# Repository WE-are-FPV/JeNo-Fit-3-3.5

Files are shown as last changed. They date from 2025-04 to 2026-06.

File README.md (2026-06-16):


> [!NOTE]
> Current version : **1.0.0** (read [changelog](#changelog) for details)

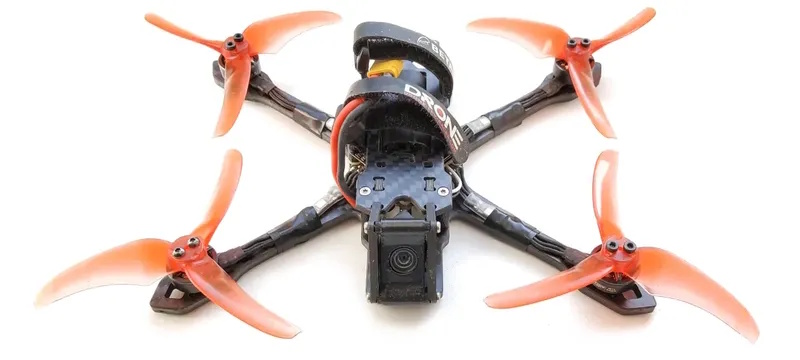
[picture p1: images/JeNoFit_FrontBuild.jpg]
JeNo Fit


# JeNo Fit 3 and 3.5"
***3 and 3.5" drone FPV frame compatible with Air Unit O4 Lite (or any Nano camera), designed for Freestyle, Freeride, bando and Cinematic.***

> [!NOTE]
> Designed in France by members of the [WE are FPV](https://www.wearefpv.fr/) community, the JeNo is already flown by hundreds of pilots and is now being sold by [Drone FPV Racer](https://www.drone-fpv-racer.com/recherche?controller=search&s=JeNo+5.1+frame&aff=64&id_campaign=13) (affiliate link). The French version of the project is available on [Printables](https://www.printables.com/model/1236372-jeno-fit-335-drone-frame). Note that a [2.5" version](https://github.com/WE-are-FPV/JeNo-Pocket), a [3-3.5" version for O4 Pro](https://github.com/WE-are-FPV/JeNo-3-3.5), a [5.1-6" version](https://github.com/WE-are-FPV/JeNo-5.1) and a [7-8" version](https://github.com/WE-are-FPV/JeNo-7) of the JeNo exist.

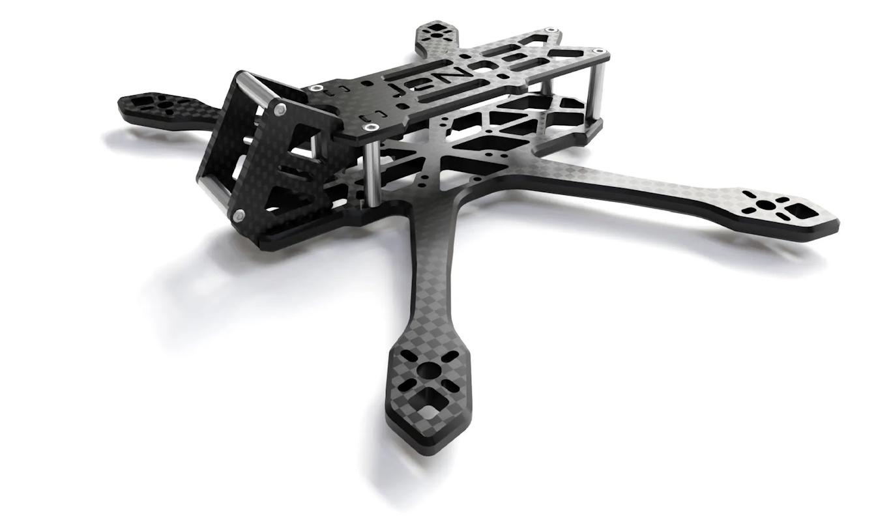
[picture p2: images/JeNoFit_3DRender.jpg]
JeNo Fit - 3D render


## Table of contents

* [Key features](#key-features)
* [Presentation](#presentation)
* [A frame available in 3 versions](#a-frame-available-in-3-versions)
* [Detailed specifications](#detailed-specifications)
* [Design: 16mm bus height – AIO only](#design-16mm-bus-height-aio-only)
* [Strategy / Motorization / Weight](#strategy-motorization-weight)
* [Blackbox](#blackbox)
* [Sturdiness](#sturdiness)
* [Versions and files](#versions-and-files)
* [Get it cut !](#buy-it-or-cut-it-)
* [Bill of materials](#bill-of-materials)
* [Inspiration](#inspiration)
* [Tuning, Betaflight Preset](#tuning-betaflight-preset)
* [Builds examples](#builds-examples)
* [Authors](#authors)
* [TPU](#tpu)
* [Community (remixes and TPU)](#community-remixes-and-tpu)
* [Changelog](#changelog)

## Key features
- [x] Perfect integration of the **DJI Air Unit O4 Lite camera**
- [x] **Wide-X** geometry
- [x] Excellent flight **performance**, easy to tune
- [x] **Sturdiness/rigidity** with a 4mm bottom plate
- [x] **100% unobstructed FOV**: Frame and standoffs invisible in the video feed
- [x] Designed for: DJI AU O4 Lite, Naked Vista (with Nebula Pro Nano), WalkSnail single board, HDZero single board, Analog
- [x] **Compact**... but not too much...
- [x] Obviously **Open Source**

## Presentation
The **DJI O4 Lite** opens up new possibilities for the 3" format: 100g builds (excluding the lipo) are once again easily achievable, with a shorter, lower, **sleeker**, and stronger frame.

The camera cage of the **JeNo Fit 3"** will therefore be designed for **Nano-sized cameras**, meaning **14mm**. 16mm standoffs slot into 1mm-deep pockets.

Of course, if you want to use an O3 or an O4 Pro, you'll need to stick with the standard [JeNo 3-3.5"](https://github.com/WE-are-FPV/JeNo-3-3.5).

But if you're ready for an O4 Lite, or even a Naked Vista, then this little JeNo Fit 3/3.5 will be much more optimal!

A small comparison between a lightweight JeNo 3" (on the right), and this new JeNo Fit 3" (on the left):
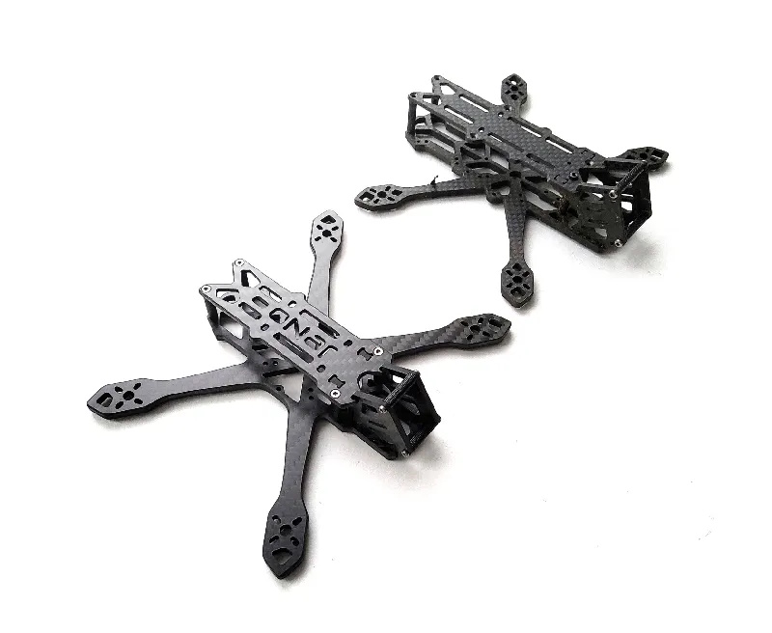
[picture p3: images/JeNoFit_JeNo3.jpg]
JeNo Fit, Fit vs Classic 3"


The JeNo is also available in [2.5" version](https://github.com/WE-are-FPV/JeNo-Pocket), [3" and 3.5" versions for O3/O4 Pro](https://github.com/WE-are-FPV/JeNo-3-3.5), [5.1-6" versions](https://github.com/WE-are-FPV/JeNo-5.1) and [7-8" versions](https://github.com/WE-are-FPV/JeNo-7).

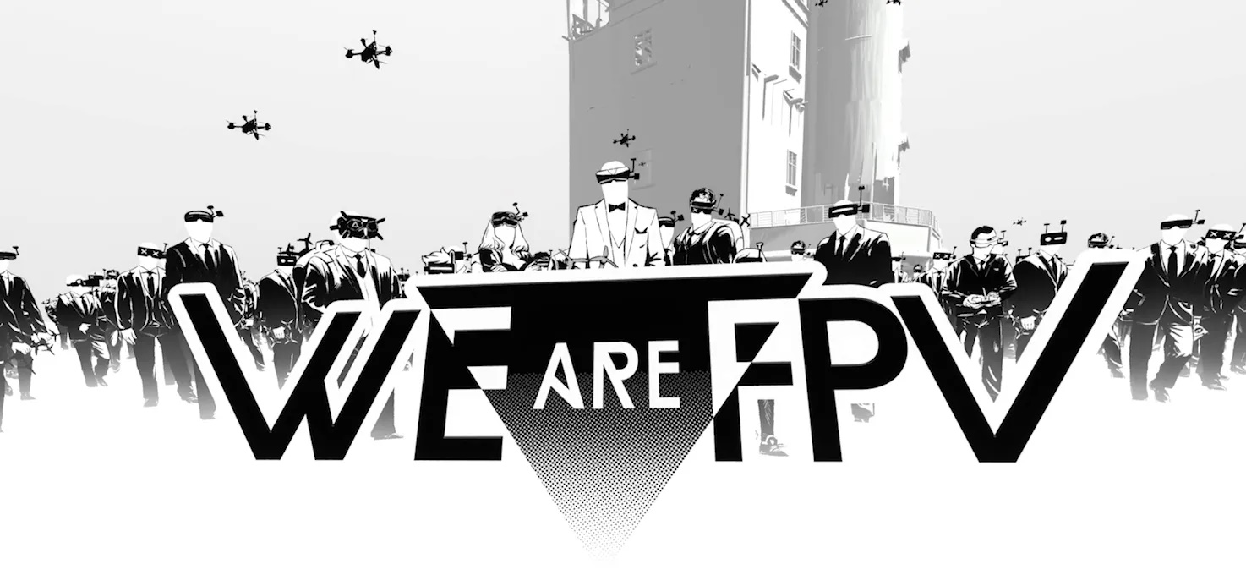
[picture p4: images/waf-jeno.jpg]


## A frame available in 3 versions
The frame is available in the following versions:

* **3.5" :** 40g with titanium screws
* **3.5" light :** 36g with titanium screws
* **3" :** 38g with titanium screws

At launch, the included **camera plates** are designed for a **30° tilt**. Other camera plates will likely be added soon (25° and 40°).

## Detailed specifications

|||
| :--- | :--- |
| **Geometry** | **Wide-X** | 
| **Props size** | 3 to 3.5" depending on the version | 
| **Weight** | **35 to 40g** depending on the version, with titanium screws | 
| **Body height** | 16 mm M2 | 
| **Bottom plate** | **4 mm** unibody | 
| **Top plate** | 2 mm | 
| **Camera plates** | 2.5 mm | 
| **Motors mounting** | 9-12 mm | 
| **Camera** | 14 mm, Nano, O4 Lite camera. **Clear FOV**. (16mm standoffs recessed) |
| **Main stack** | AiO 25.5 mm x 25.5 mm (M2) and 20 mm x 20 mm (M2) | 
| **Supported VTX** | Analogic, **DJI Air Unit O4 Lite**, WalkSnail, HDZero… | 
| **Strap passage** | Yes | 

## Design: 16mm bus height – AIO only
For the electronics, only AiOs will be accepted. However, they can have the USB port either horizontally or vertically, while keeping the USB port protected.

There will be enough space for an external RX and/or capacitor at the rear and front.

For builds using a Naked Vista, it is recommended to tape the underside of the top plate to prevent short circuits due to contact with the carbon (the build remains relatively tight).

AiO with vertical USB: (AiO rotated 90°)

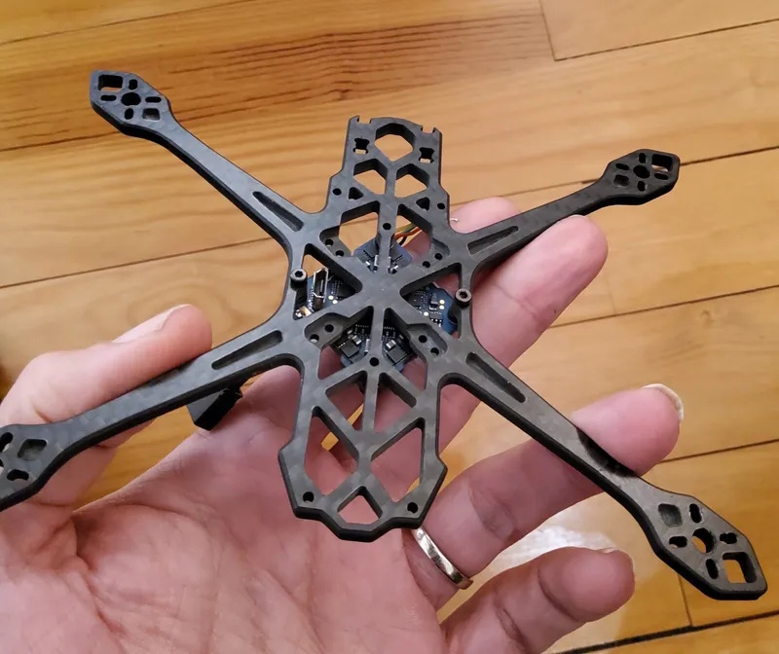
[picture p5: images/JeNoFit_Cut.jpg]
JeNo Fit, RX options


| 3" Naked Vista build | 3.5" O4 "light" build |
| :---: | :---: |
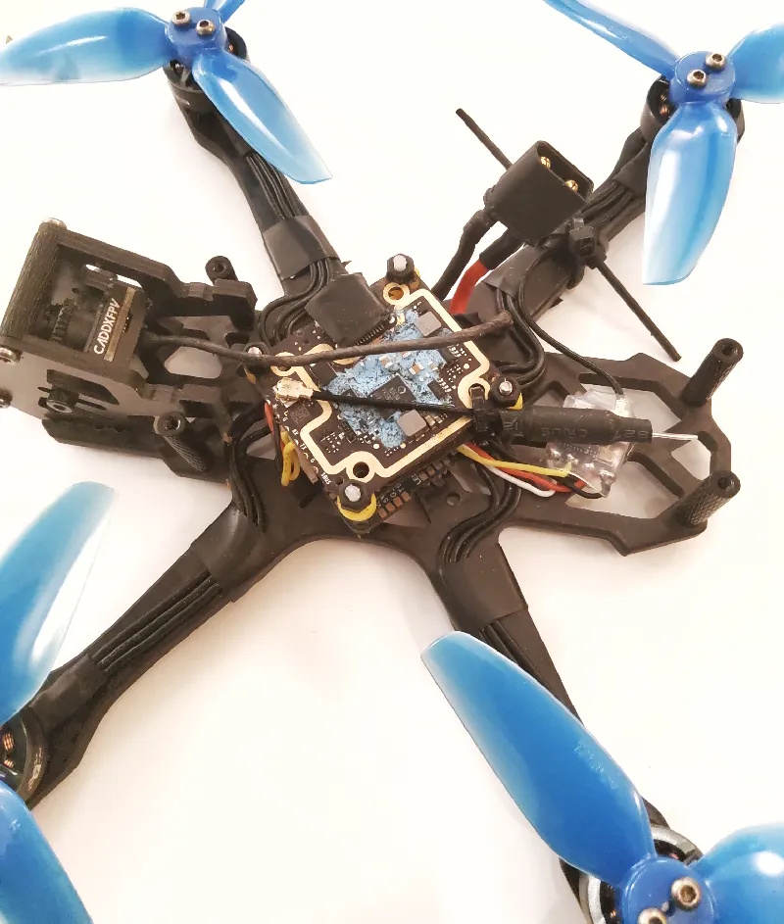
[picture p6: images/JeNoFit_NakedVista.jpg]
Freestyle camera plates
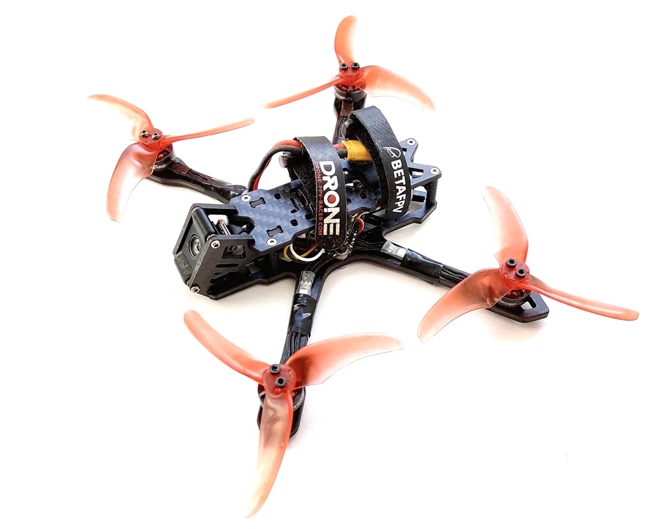
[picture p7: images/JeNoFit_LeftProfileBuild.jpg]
Cinematic camera plates
|  |  |

## Strategy / Motorization / Weight

Several strategies are available to you:

* **3" or 3.5"**, with a wide range of motor options depending on what you want to achieve: from **1204 to 1604**. This choice will have a significant impact on the build's weight, behavior, and flight time.
* If you're looking for **discretion** while maintaining optimal cruising speed, the 1204 will be perfect in **3.5"**, between **5000 and 6000kv** for **3S**. The sound of the Emax Avan 3528 props will remain discreet at lower RPMs.
* If you're after **punch, the **1604** should be perfect for **4S**.
  * **1604 = 46g** motors
  * **1204 = 24g** motors

| 1204 | 1404 | 1604 |
| :---: | :---: | :---: |
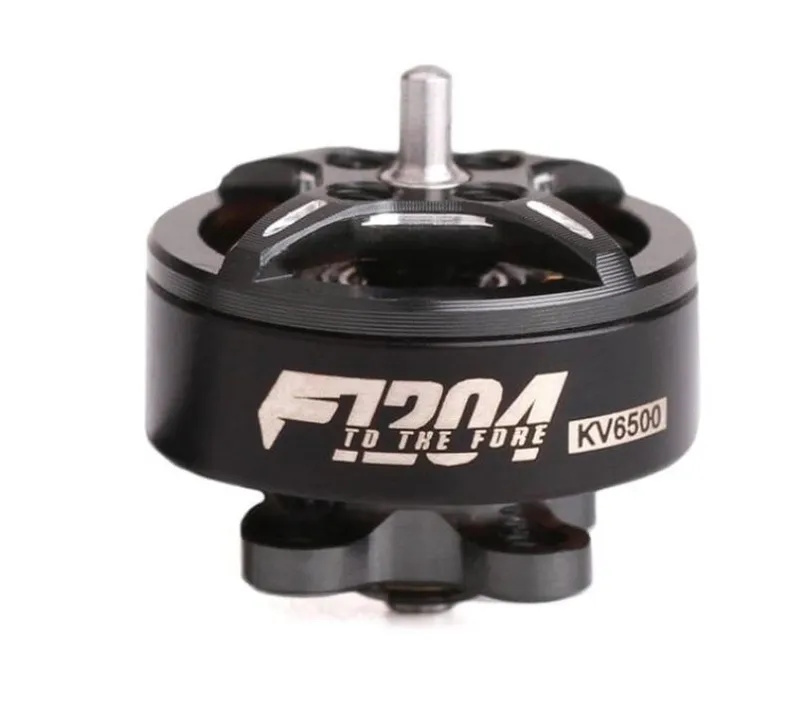
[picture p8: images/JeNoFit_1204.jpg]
1204 motor
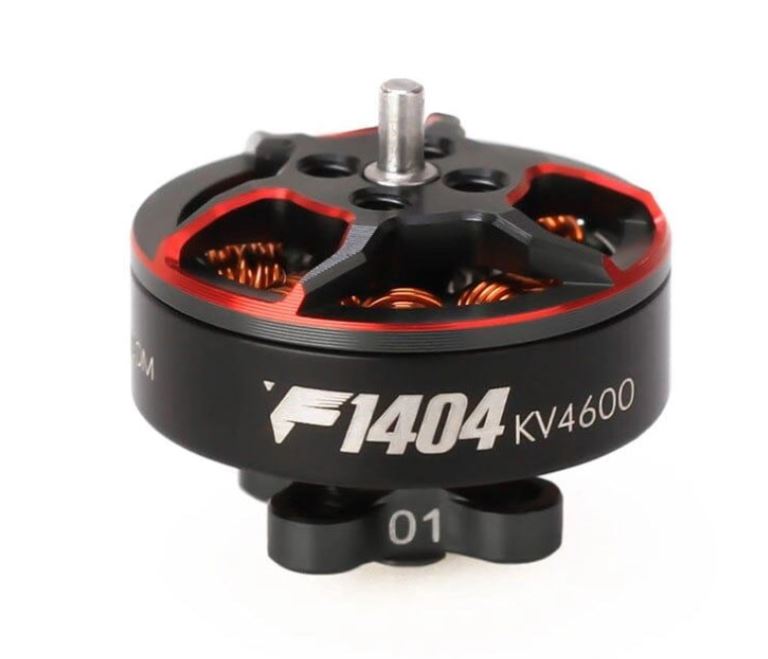
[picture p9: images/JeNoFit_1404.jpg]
1404 motor
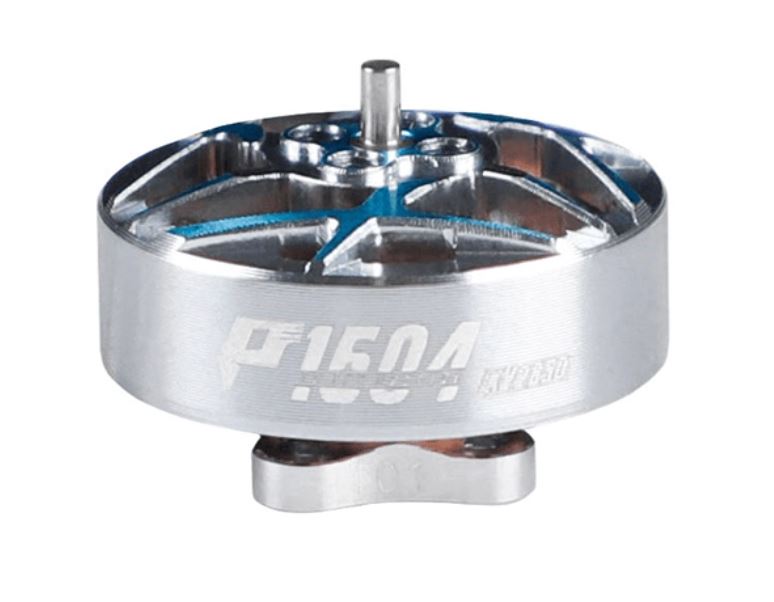
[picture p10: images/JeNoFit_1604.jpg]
1604 motor
|  |  |  |
| 6.9gr (incl cable) | 9.3gr (incl cable) | 11.6gr (incl cable) |

You will therefore be looking at a build around 95/100g with 1204 motors, versus 122g with 1604 motors.

1204 and Naked Vista build at 99g:
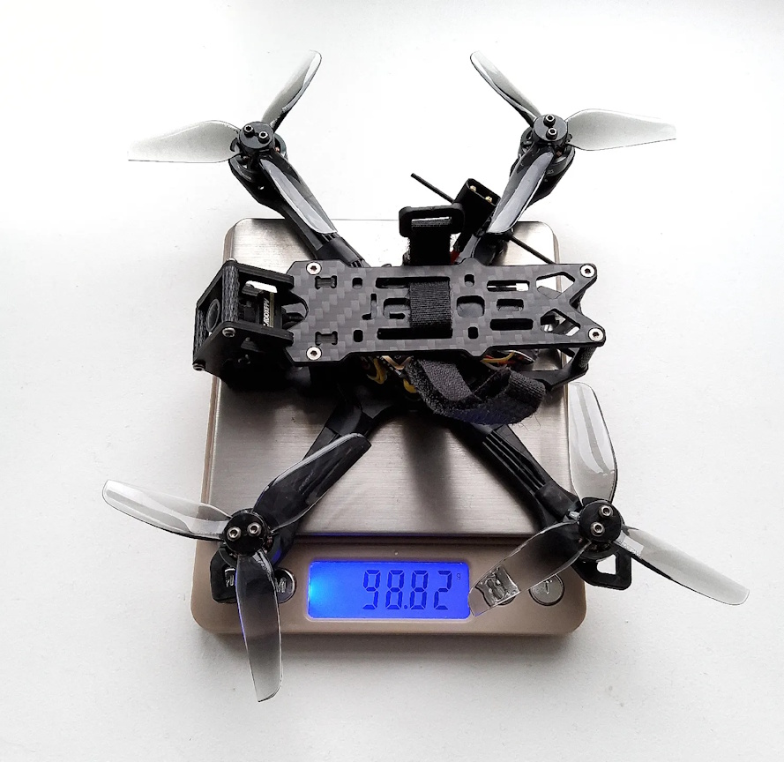
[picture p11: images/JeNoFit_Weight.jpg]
JeNo Fit weight
  |
 
## Blackbox

The 4mm bottom plate ensures a clean BB.

Here is an excerpt of the BB in 3.5" / 1204:

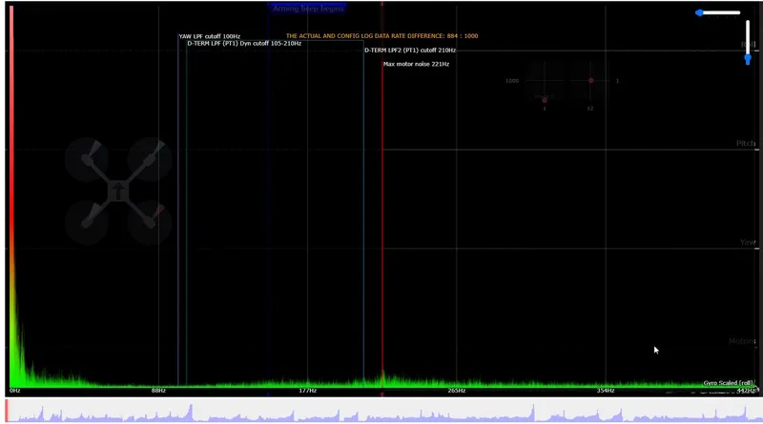
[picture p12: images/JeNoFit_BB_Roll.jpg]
JeNo Fit Blackbox roll

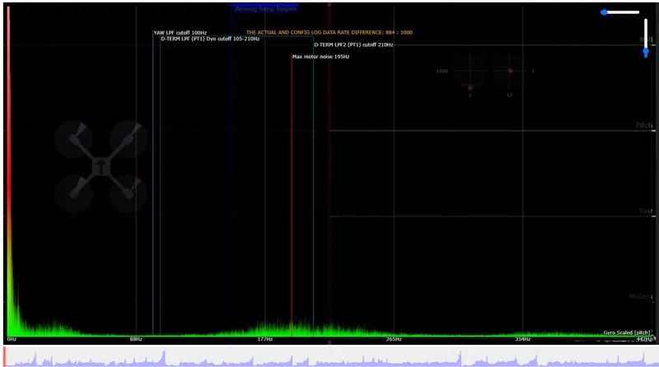
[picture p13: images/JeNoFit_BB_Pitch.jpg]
JeNo Fit Blackbox pitch

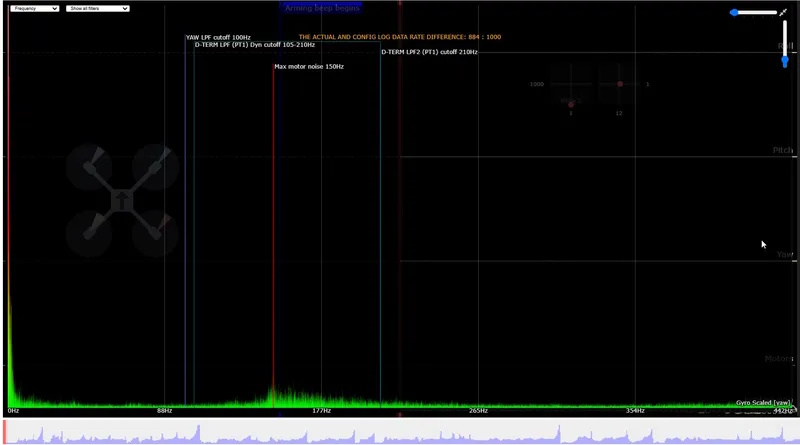
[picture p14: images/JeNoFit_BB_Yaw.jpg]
JeNo Fit Blackbox yaw


## Sturdiness
The build is **lighter** than a standard JeNo 3. The **bottom is shorter** but still **4mm** thick, so we’re not concerned about the frame's durability. Remember to grab the arm protection from the [JeNo 3"](https://github.com/WE-are-FPV/JeNo-3-3.5) if you're doing bando.

## Versions and files

### Versioning
You will find the **current version** of the frame at the beginning of the description and the full [history of modifications](#changelog) at the end of the page.

We strongly recommend always cutting the latest version to ensure you benefit from the most recent optimizations.

The version **number format** is as follows :
```
<Major versions>.<Minor version>.<Revision>
ex : 1.3.2
```

* **Revision :** This number is incremented in the case of minor modifications with no significant impact.
* **Minor version :** This number is incremented for minor modifications that may potentially break compatibility with certain TPU parts.
* **Major version :** This number is incremented for significant modifications that break compatibility at the carbon level.

Since the creation of the JeNo 5", we have always strived to **maintain compatibility at the carbon level**. As a result, the version remains “1.x.y.”

**Note :** If you develop TPU parts for the JeNo, be sure to specify the version they are compatible with.

### Files management
To simplify things, we have reorganized the file structure. The files are now divided into **five groups** :

* **01-FRAME :** Contains **models** describing the **frame** in DXF, STEP, and STL formats for the current version. Also contains a PDF file which is a reformatted version of the DXF.
* **02-TPU :** Contains **TPU models** for the current frame version in STL format.
* **03-FRAME-HISTORY :** Contains previous versions of the frame.
* **04-TPU-HISTORY :** Contains TPU models that are no longer compatible with the current version.
* **OTHER-FILES :** Contains documentation files, including the assembly manual and a description.

The major change is that all options are now consolidated into a single file. This will make version management significantly easier for us.

If you want to view the DXF file with all annotations, we recommend using the free software [DWG TrueView](https://www.autodesk.com/products/dwg-trueview/overview). If you prefer not to use it, the PDF version of the file will contain all the necessary information.

## Get it cut !

JeNo Fit, cut

The JeNo Fit 3/3.5" is available at [FPV CNC Drone](https://fpvcncdrone.com/).

Unlike the 3 and 5" JeNos, the JeNo Fit won't be available in shops.

The ["01-FRAME"](https://github.com/WE-are-FPV/JeNo-Fit-3-3.5/tree/main/01-FRAME) folder contains all the files you need to get it **cut**. .DXF and .STEP files are available.

## Bill of materials

In addition to the carbon fiber, you will need the following hardware to complete the assembly of the frame.

**Standoffs**

It is recommended to use 5mm diameter standoffs, especially for those that will serve as support for TPU (backpack and capacitor). Moletted spacers can still be used, but the TPU supports will need to be modified accordingly.

| Quantity | Description | Details |
| :---: | :--- | :--- |
| **4** | **M2x16mm** standoffs **(4 mm diameter)** | for the body |
| **2** | **M2x16mm** standoffs **(4 mm diameter)** | for the camera (14mm) |

> [!NOTE]
> The standoffs for the camera plates are recessed by 1mm on each side to standardize the hardware. If you have 14mm standoffs, you can use them by having custom camera plates made without the 1mm pockets.

**Stack materials**

20mm screws will comfortably accommodate most configurations. You can use shorter screws if you prefer.
| Quantity | Description | Details |
| :---: | :--- | :--- |
| **4** | **M2x16/18mm** screws | for the stack |
| **8** | **M2** nylon nuts for the stack screws (4 nuts for the base, 4 nuts on top) | for the stack |

**Frame materials**

| Quantity | Description | Details |
| :---: | :--- | :--- |
| **4** | **M2x6/8mm countersunk screws** (titanium if possible) | for the top plate |
| **8** | **M2x8mm screws** screws (titanium if possible) | for the bottom and camera plates |

**Additional materials**

| Quantity | Description | Details |
| :---: | :--- | :--- |
| **12-16** | **M2x6mm** screws if there is NO arm protection between the screw and the motor, otherwise, **M2x7mm**. To save **weight**, you can use only **3 screws per motor**. | for the motors |

## Inspiration

The **JeNo Fit** is primarily inspired by its bigger brother, the [standard JeNo 3"](https://github.com/WE-are-FPV/JeNo-3-3.5). Like the [JeNo Fit](https://github.com/WE-are-FPV/JeNo-Pocket), it is designed for a Nano-sized camera.

**Gone is the rear stack**, which is no longer needed with the Air Unit O4 Lite. The front, made up of 2 camera plates, was designed around the O4 Lite camera.

## Tuning, Betaflight Preset

**No preset integrated for now.** The behavior of the AiOs can vary quite a bit from one to another. We’ll wait for more feedback.

However, here’s an overview of the first tune used for our test flights, which you can use as a starting point if your **Blackbox is clean enough**. Note that we’ve activated the profile switch based on the number of cells in the lipo.

As always, be very **cautious** when applying these settings.

## Builds examples

You can find several build examples in the Dronebuilds section of the WE are FPV forum:

* [Jeno 3 Low Profil O4](https://forum.wearefpv.fr/topic/24231-jeno-3-low-profil-o4) (by Tooks)

## Authors

The JeNo Fit was designed by :

* nochamo - [Youtube](https://www.youtube.com/user/nochamo)

## TPU

Among the files to download, you’ll find some TPU parts for your JeNo Fit. Initially, these include only the camera/antenna mounts for 4 mm standoffs.

## Community (remixes and TPU)

**Fork/remix**

If something isn't 100% to your liking on the JeNo Fit, feel free to check out the community remixes—you might just find what you're looking for:

**TPU**

## Changelog

> [!TIP]
> Compatibility is consistently maintained between each version: if your frame was a v1, the parts from v1.2 will be compatible. The same applies to TPU accessories. That's why we don't keep the history of previous versions.

* Version **1.0.0** (01/02/2025) :
  * Release of the JeNo Fit

## Join the JeNo family !

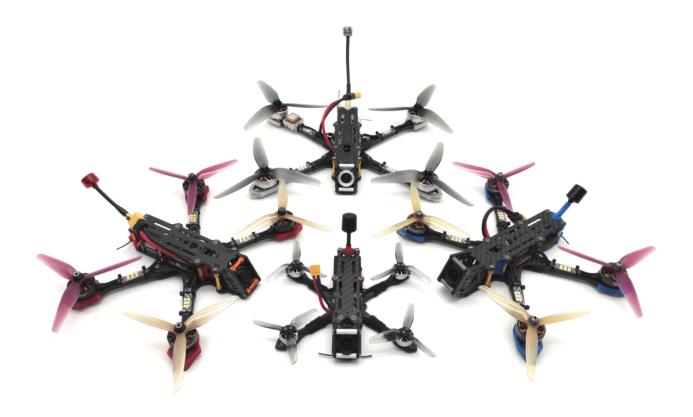
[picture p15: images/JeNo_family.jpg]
||
|:---:|
| JeNo Classic Modus (left), JeNo Cine (right), JeNo 6" (top), JeNo 3" (bottom) |

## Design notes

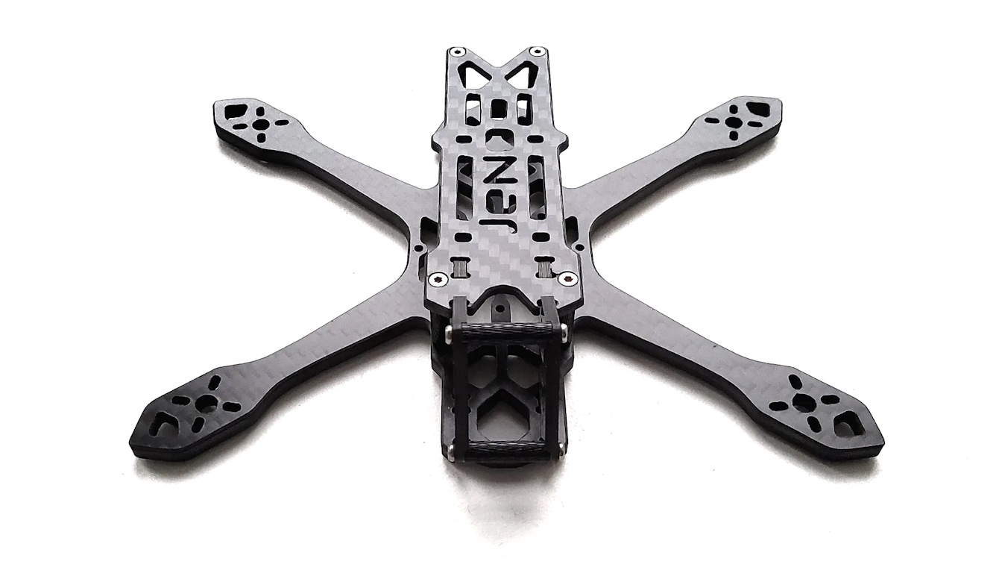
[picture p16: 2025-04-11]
images/JeNoFit_Front.jpg

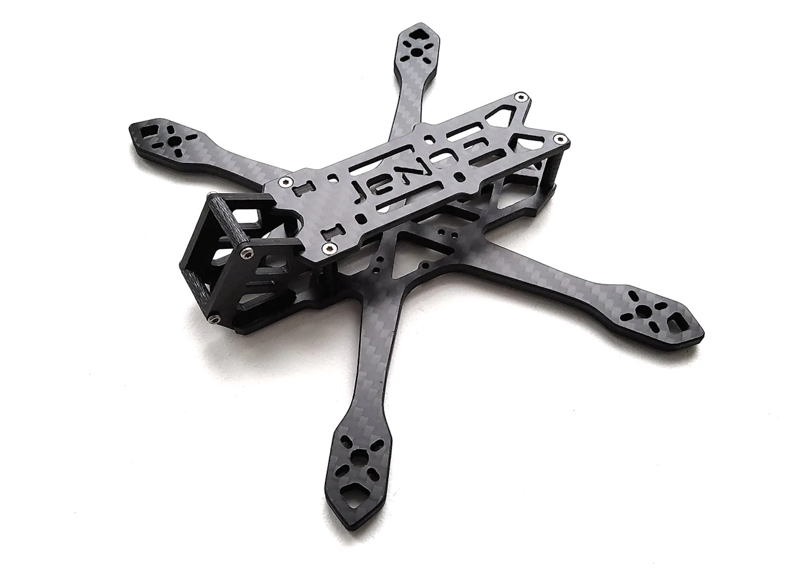
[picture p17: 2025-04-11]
images/JeNoFit_Profile.jpg

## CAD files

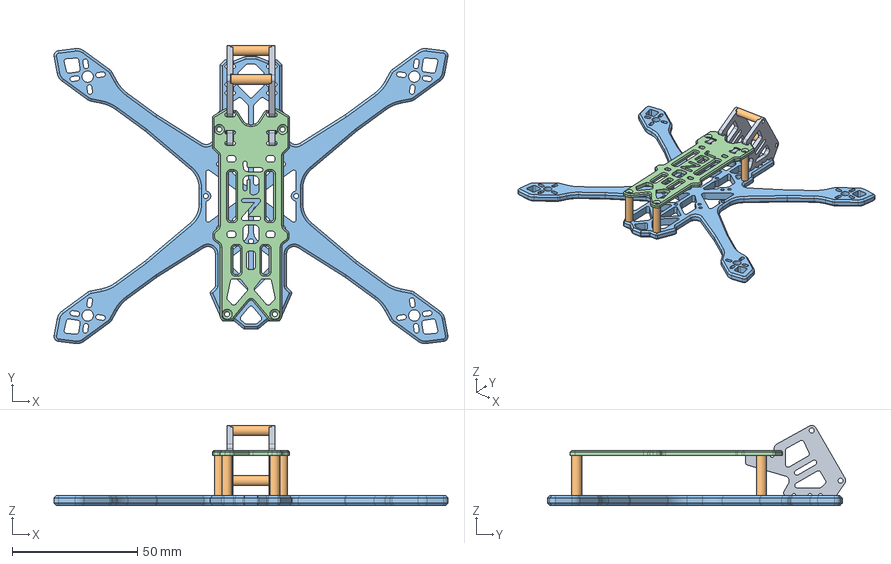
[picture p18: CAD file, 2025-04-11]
01-FRAME/JeNoFit_ALL_VERSIONS_1.0.0.step
157.1 x 118.9 x 31.9 mm

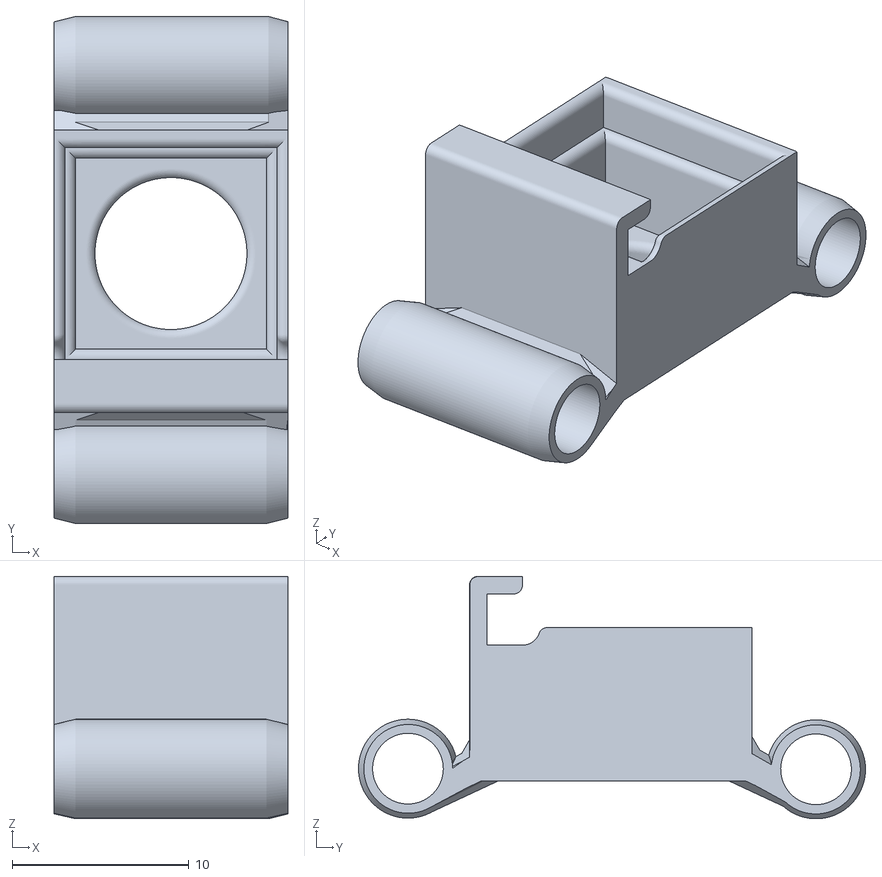
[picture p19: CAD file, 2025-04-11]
02-TPU/JeNoFit_1.0_O4_Lite_Mount_4mm_Standoffs.stl
13.2 x 28.7 x 13.7

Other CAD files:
01-FRAME/JeNoFit_Preview.stl
01-FRAME/JeNoFit_ALL_VERSIONS_1.0.0.dxf

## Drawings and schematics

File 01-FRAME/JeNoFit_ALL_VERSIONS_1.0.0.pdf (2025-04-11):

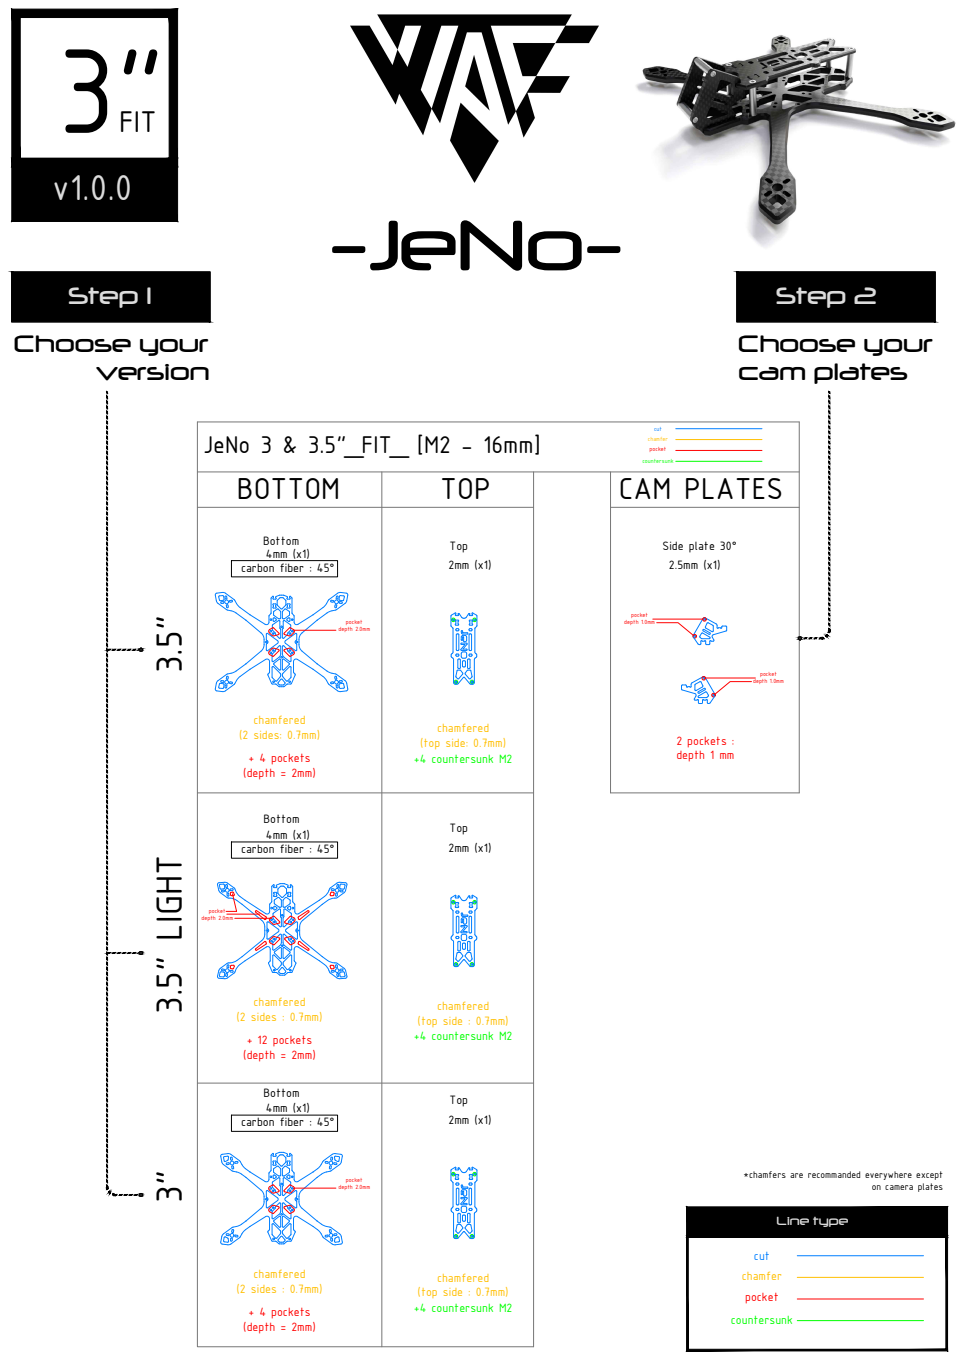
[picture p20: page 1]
(top side: 0.7mm); 2 pockets : depth 1 mm; carbon fiber : 45°; + 4 pockets (depth = 2mm); depth 2.0mm; (2 sides: 0.7mm); +4 countersunk M2; + 12 pockets (depth = 2mm); (2 sides : 0.7mm); (top side : 0.7mm); +4 countersunk M2 3.5" 3.5" LIGHT; 4mm (x1) carbon fiber : 45° 3"; Choose your; Choose your cam plates; Step 1 Step 2; Line type

JeNo 3 & 3.5"_FIT_ [M2 - 16mm] | cut chamfer pocket countersunk
BOTTOM | TOP | CAM PLATES

Bottom 4mm (x1) | Top 2mm (x1) | Side plate 30° 2.5mm (x1) pocket depth 1.0mm pocket depth 1.0mm

*chamfers are recommanded everywhere except

on camera plates

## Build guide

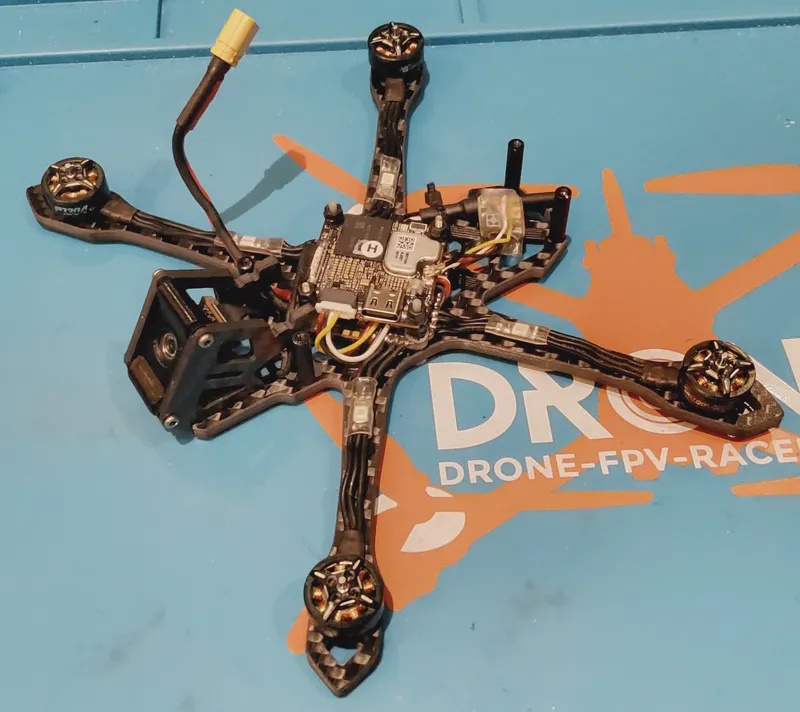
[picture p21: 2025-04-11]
images/JeNoFit_OpenBuild.jpg

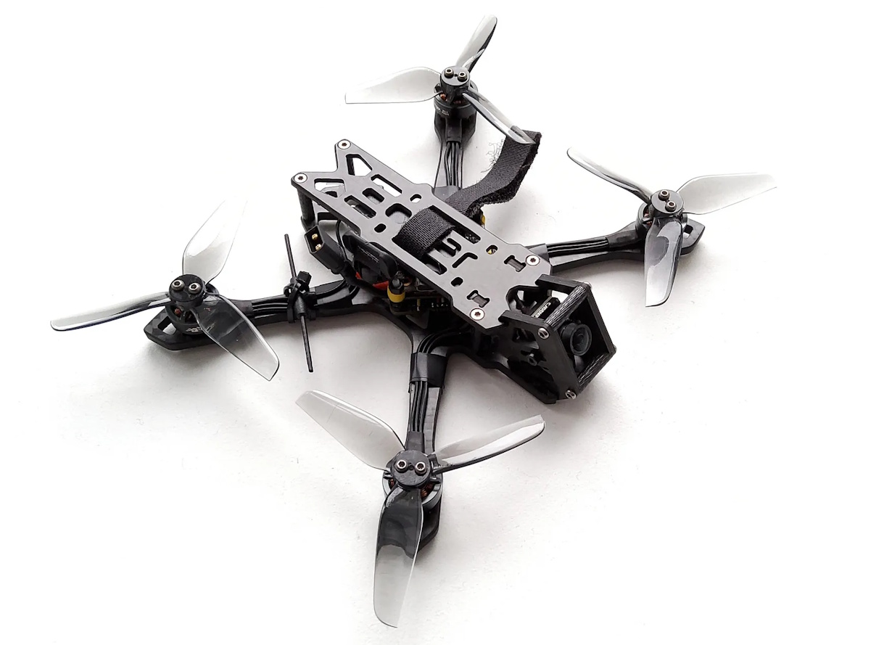
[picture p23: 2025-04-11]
images/JeNoFit_RightProfileBuild.jpg

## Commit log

2025-04-11 Init JeNot Fit
    [JeNoFit_1.0_O4_Lite_Mount_4mm_Standoffs.stl, JeNoFit_ALL_VERSIONS_1.0.0.dxf, JeNoFit_ALL_VERSIONS_1.0.0.step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]
2025-09-02 Apply line ending normalization for DXF
    [JeNoFit_ALL_VERSIONS_1.0.0.dxf]

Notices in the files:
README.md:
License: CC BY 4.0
